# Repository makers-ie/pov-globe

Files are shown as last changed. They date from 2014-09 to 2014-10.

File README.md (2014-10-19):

PoV Globe
=========

Persistence of vision globe project.

Requirements
------------
* Use an FPGA
* The size should be noticable
* Rotation should be well balanced
* Should be easy to interface with from a PC

Design
------
* One ring of LEDs, stuck on a pivoting axis.
* Ring diameter 50 cm is noticable.
* Stepper motor to drive the ring, for speed control.
* Encoder to avoid drifting.
* RGB LEDs
* Stick LEDs on both halves of the ring for better balance.
* Shift LEDs on one half one half-LED for increased resolution.
* Use wireless for interfacing, so we don't have to transfer high-bandwidth data to the rotor.
  * Bluetooth module is suggested.
  * NRF24L01 pair with Teensy USB interface suggested.
* Build PCB ring segments with SMD LEDs mounted on the edge.

Limits
------
* Ring diameter 50 cm; circumference 1.6 m
* PLCC4 RGB LEDs are 3.5x2.8 mm; maximum resolution is 9 dpi
* With interlacing; maximum resolution is 18 dpi
* At 18 dpi, would use 535 LEDs
* Divide circle into **16** sectors, ignore the two bottom sectors
* Each sector has 32 LEDs, for a total of 64 LEDs ignored
* In total, we have **448** LEDs
* Control for RGB needs 1,344 channels
* Spin ring at 60 rps
* We should have the same resolution both horizontally and vertically
* Each slice must update 1,344 channels
* FPGA board has **42** I/O pins
* Divide channels into matrix of 32x42
* With a shift-register column driver, this requires **34** FPGA connections
* Each slice must update 42 columns; FPGA scans at 1.3 MHz
* With RGB555; 32 shades per base color; FPGA runs PWM at **42 MHz**
* With RGB555; framebuffer memory is 572 kB; with double-buffering **1.14 MB**

Mechanical
----------
* A ring divided into 16 sectors, each with a PCB
* Cross-bars horizontally and vertically for rigidity
* Stepper-motor located in center of ring to avoid unbalanced twisting forces
* Plastic fasteners to attach cross-bars to stepper motor and ring PCBs
* Ring PCBs on one side shifted 1/2 LED for interlacing
* Foundation in reinforced concrete with a fixed steel axis extending to the stepper motor
* Steel axis connected to stepper motor with locking pin?
* FPGA board located in the lower part of the ring to utilize the space created by not having LED PCBs there
* Stepper motor driver could be counter-weight for FPGA board
* One (or two?) ball bearings in the lower ring part
* Ball bearings inside copper pipe or plastic to make it easy to fasten the ring PCBs and FPGA
* We can run ground in the fixed steel axis, unless the stepper motor is weird
* If one ball bearing is insulated from the fixed axis, the other pole can go through the bearing
* Hall/optical-sensor for motor auto-calibration (1 pulse/revolution)
* Ring PCBs
  * Copper traces going to the edge, connecting by direct soldering should be rigid and good
  * We will be running MHz signals, so 4-layer PCB is probably needed to have a full ground plane

Electrical
----------
* We should be fine with 5 V
  * FPGA board needs Vcc = 5 V
  * LEDs are Vf <= 3.5 V
  * Stepper motor (42BYGHW609, NEMA 17?) needs 3.4 V (resistive)
* Current usage is max 3 A
  * FPGA likely less than 100 mA
  * LEDs are Ifm < 32*25 mA < 1 A
  * Stepper motor can do 1.7 A (resistive)
* Power usage is max 15 W
* Components
  * Stepper motor driver
  * Power supply 5V/15W
  * Ring sector PCBs x14
  * FPGA interface PCBs x2
    * Ring-side PSU filter
    * Hall/optical-sensor
    * Stepper motor driver
    * LED row drivers
* Each ring PCB will have 32x3 channels
  * With 16 rows, this means 6 columns
  * We split the PCB in two column groups and drive each color as a column, i.e. a 2x3 column configuration
  * Need a 6-bit high-speed shift register, f <= 42 MHz, 23 ns per cycle
  * Prefer ICs that can drive 25 mA LEDs by themselves
  * Candidate is [74VHC595](http://www.fairchildsemi.com/ds/74/74VHC595.pdf), Iout <= 25 mA, Vcc <= 5.5 V, f <= 155 MHz
* FPGA I/O, 48 max
  * 1 Rotation sensor (analog?)
  * 2 LED columns (clock, data)
  * 3 Communications (SPI)
  * 4 Stepper motor output (Bipolar H-bridge)
  * 32 LED rows
  * Max IOH 24 mA when using LVCMOS33 outputs. [Datasheet](http://www.xilinx.com/support/documentation/data_sheets/ds162.pdf), page 10.

Datasheets
----------
These are components which we already have:

* Controller: [Spartan LX9](http://www.xilinx.com/support/documentation/data_sheets/ds160.pdf), 32Mhz oscillator, 48 GPIO pins, 64Mbit SDRAM, 64Mbit Flash
  * [Store](http://store.gadgetfactory.net/papilio-pro)
  * [Pinouts](http://papilio.cc/index.php?n=Playground.PapilioPinouts)
* RGB LED: [PLCC4RGBCT-CA](http://www.hebeiltd.com.cn/led.datasheet/PLCC4RGBCT-CA.pdf)
* RF transceiver: [nRF24L01](http://www.nordicsemi.com/eng/content/download/2726/34069/file/nRF24L01P_Product_Specification_1_0.pdf)
  * [Module](http://www.aliexpress.com/item/2pcs-lot-NRF24L01-2-4GHz-Wireless-Transceiver-Module-for-Arduino-Microcontroller-Free-Shipping/1836172303.html)

Candidates for new parts:

* PSU: [AS-25-5](http://www.aliexpress.com/item/25W-5V-Small-Volume-Single-Output-Switching-power-supply-for-LED-Strip-light/628334432.html)
* PSU: [HR-090505A](http://www.aliexpress.com/item/AC-DC-Adapter-5V-5A-DC-Plug-Size-5-5x2-5mm-Power-Adapter-Charger-Switching-with/1060711434.html)
* Stepper motor: [42BYGHW609](http://www.aliexpress.com/item/Best-Selling-5-PCS-Wantai-4-lead-Nema-17-Stepper-Motor-42BYGHW609-56oz-in-40mm-1/599005546.html)
* Motor driver stage: [L298](http://www.st.com/st-web-ui/static/active/en/resource/technical/document/datasheet/CD00000240.pdf)

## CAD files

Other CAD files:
mechanical/pov-globe.skp

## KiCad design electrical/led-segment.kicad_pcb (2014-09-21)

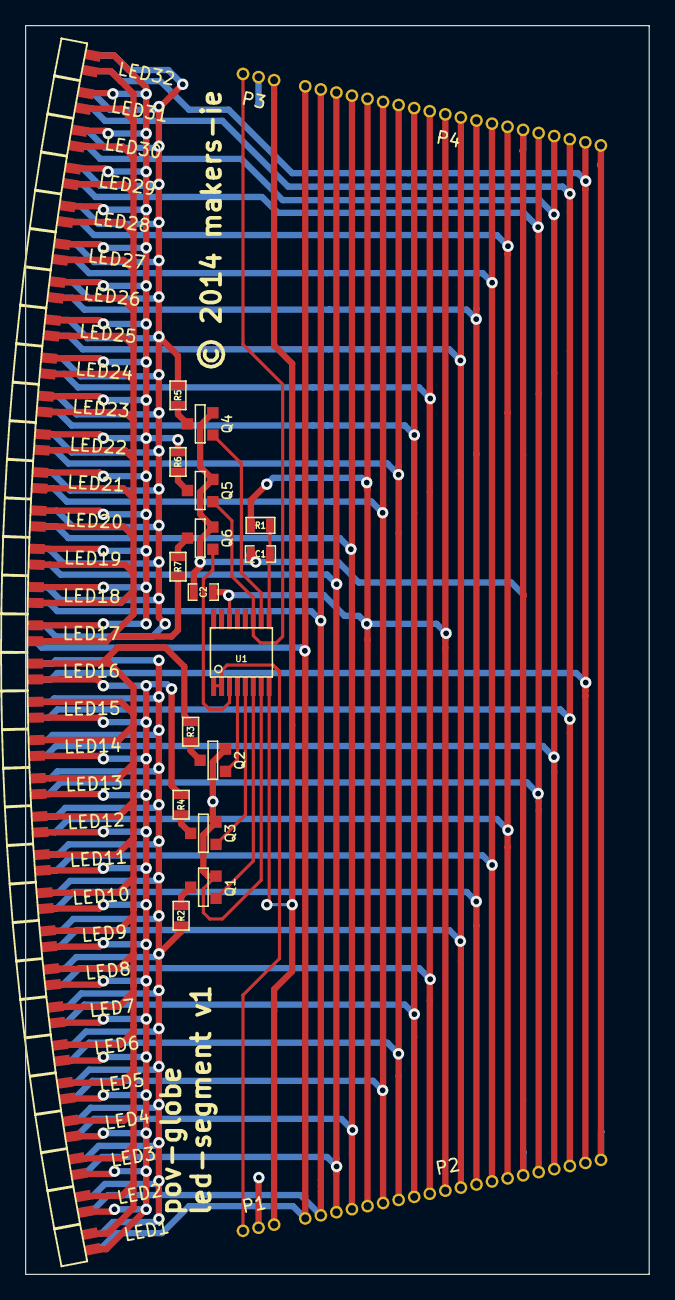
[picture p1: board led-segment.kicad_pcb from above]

Board: 2 copper layers, 49.9 x 99.9 mm, 52 parts (0 on the bottom side), 39 nets.

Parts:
C1, C2: C; SM0603_Capa
LED1, LED2, LED3, LED4, LED5, LED6, LED7, LED8, LED9, LED10, LED11, LED12, LED13, LED14, LED15, LED16, LED17, LED18, LED19, LED20, LED21, LED22, LED23, LED24, LED25, LED26, LED27, LED28, LED29, LED30, LED31, LED32: PLCC4RGBCT-CA; plcc4-edge
P1, P3: CONN_3; boardedge_3
P2, P4: CONN_20; boardedge_20
Q1, Q2, Q3, Q4, Q5, Q6: FDV301N; SOT23GDS
R1, R2, R3, R4, R5, R6, R7: R; SM0603
U1: 74164; ssop-16

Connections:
+5V: C2.1, P2.5, P2.10, P4.5, P4.10, R1.1, U1.14
/8xLED group A/LCB: LED1.3, LED2.3, LED3.3, LED4.3, LED5.3, LED6.3, LED7.3, LED8.3, LED9.3, LED10.3, LED11.3, LED12.3, LED13.3, LED14.3, LED15.3, LED16.3, R2.1
/8xLED group A/LCG: LED1.4, LED2.4, LED3.4, LED4.4, LED5.4, LED6.4, LED7.4, LED8.4, LED9.4, LED10.4, LED11.4, LED12.4, LED13.4, LED14.4, LED15.4, LED16.4, R3.1
/8xLED group A/LCR: LED1.1, LED2.1, LED3.1, LED4.1, LED5.1, LED6.1, LED7.1, LED8.1, LED9.1, LED10.1, LED11.1, LED12.1, LED13.1, LED14.1, LED15.1, LED16.1, R4.1
/8xLED group C/LCB: LED17.3, LED18.3, LED19.3, LED20.3, LED21.3, LED22.3, LED23.3, LED24.3, LED25.3, LED26.3, LED27.3, LED28.3, LED29.3, LED30.3, LED31.3, LED32.3, R5.1
/8xLED group C/LCG: LED17.4, LED18.4, LED19.4, LED20.4, LED21.4, LED22.4, LED23.4, LED24.4, LED25.4, LED26.4, LED27.4, LED28.4, LED29.4, LED30.4, LED31.4, LED32.4, R6.1
/8xLED group C/LCR: LED17.1, LED18.1, LED19.1, LED20.1, LED21.1, LED22.1, LED23.1, LED24.1, LED25.1, LED26.1, LED27.1, LED28.1, LED29.1, LED30.1, LED31.1, LED32.1, R7.1
/LRA0: LED1.2, LED17.2, P2.1, P4.1
/LRA1: LED2.2, LED18.2, P2.2, P4.2
/LRA2: LED3.2, LED19.2, P2.3, P4.3
/LRA3: LED4.2, LED20.2, P2.4, P4.4
/LRA4: LED5.2, LED21.2, P2.6, P4.6
/LRA5: LED6.2, LED22.2, P2.7, P4.7
/LRA6: LED7.2, LED23.2, P2.8, P4.8
/LRA7: LED8.2, LED24.2, P2.9, P4.9
/LRB0: LED9.2, LED25.2, P2.11, P4.11
/LRB1: LED10.2, LED26.2, P2.12, P4.12
/LRB2: LED11.2, LED27.2, P2.13, P4.13
/LRB3: LED12.2, LED28.2, P2.14, P4.14
/LRB4: LED13.2, LED29.2, P2.16, P4.16
/LRB5: LED14.2, LED30.2, P2.17, P4.17
/LRB6: LED15.2, LED31.2, P2.18, P4.18
/LRB7: LED16.2, LED32.2, P2.19, P4.19
GND: C1.2, C2.2, P1.2, P2.15, P2.20, P3.2, P4.15, P4.20, Q1.S, Q2.S, Q3.S, Q4.S, Q5.S, Q6.S, U1.7
unnamed: C1.1, R1.2, U1.9
unnamed: P1.1, U1.1, U1.2
unnamed: Q3.D, R4.2
unnamed: Q2.D, R3.2
unnamed: Q1.D, R2.2
unnamed: P1.3, P3.3, U1.8
unnamed: Q6.G, U1.3
unnamed: P3.1, Q5.G, U1.11
unnamed: Q4.G, U1.10
unnamed: Q1.G, U1.6
unnamed: Q3.G, U1.5
unnamed: Q2.G, U1.4
unnamed: Q6.D, R7.2
unnamed: Q5.D, R6.2
unnamed: Q4.D, R5.2

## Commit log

2014-06-16 Add datasheets and descriptions of what we currently have as an FPGA board.
2014-06-16 Add initial mechanical model.
    SketchUp for now.
    [pov-globe.skp]
2014-06-17 Fill in ring PCB suggestion, stepper motor and PSU datasheets.
2014-06-17 Make proper Papilio Pro mechanical model.
    Also shifts half-ring one half-LED.
    Adds interface boards at the bottom.
    [pov-globe.skp]
2014-06-22 Add initial electrical schema.
    Uses KiCad. stepper drivers.lib downloaded from www.kicadlib.org/.
    [led-row-driver.sch, pov-globe.sch]
2014-06-29 Add LED segment schematic.
    [8led-group.sch, led-row-driver.sch, led-segment.sch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]
2014-07-24 Add genledsegmentpcb.
    A script to place LED modules and generate the board outline
    with good accuracy. The output is meant to be used as a starting
    point for manual modifications.
2014-07-24 Add generated led-segment PCB.
    [led-segment.kicad_pcb]
2014-07-24 Add hb.lib and hb.mod.
    [8led-group.sch, led-row-driver.sch, led-segment.sch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]
2014-07-24 Small Sketchup fixup.
    [pov-globe.skp]
2014-07-25 Add footprint filter for nrf24l01.
2014-07-25 Split led-segment.sch away from pov-globe.sch.
    They are on separate PCBs and netlist generation is per-schema.
    [8led-group.sch, led-row-driver.sch, led-segment.sch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]
2014-07-25 Add edge connectors to PCB template and fix up LED label alignment.
2014-07-27 Center led-segments PCB in Y direction.
2014-07-29 Add driver transistors to led-segment. Replace 74595.
    [8led-group.sch, led-segment.sch]
2014-07-29 Add boardedge connectors.
2014-07-29 Fix boardedge_20 pad 1 position.
2014-07-29 Fix ERC warnings for led-segment.
    [8led-group.sch, led-segment.sch]
2014-07-29 Add led-segment.cmp.
2014-07-29 Add led-segment decoupling capacitor. Rewire for PCB layout.
    Rewire transistors to have a better PCB layout.
    [8led-group.sch, led-segment.sch]
2014-07-29 Route led-segment board.
    Should be complete now.
    [led-segment.kicad_pcb]
2014-07-29 Change led-segments PCB to A4.
    [led-segment.kicad_pcb]
2014-07-30 Change places of p3 and p20 connectors.
    We need more space for the column driver IC.
    Fix pad 1 on p20.
2014-07-30 Enlarge boardedge pads. Small track fixups.
    [led-segment.kicad_pcb]
2014-09-14 Add led-segment ground plane. Convert to two layer.
    [led-segment.kicad_pcb]
2014-09-14 Ignore Kicad backup files.
2014-09-21 Move led-segment text to silk screen. Add 50x100 mm edge cut.
    [led-segment.kicad_pcb]
2014-09-21 Add prod/led-segment.zip. Version 1 for seeedstudio.
2014-09-21 Increase all vias to 36/20 mil mil.
    [led-segment.kicad_pcb]
2014-10-19 Add FPGA output current data.

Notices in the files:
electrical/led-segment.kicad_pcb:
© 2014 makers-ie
